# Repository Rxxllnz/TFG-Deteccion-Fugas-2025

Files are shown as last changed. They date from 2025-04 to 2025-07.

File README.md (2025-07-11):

# Detección de Fugas

Este Trabajo Fin de Grado documenta el proceso de puesta en funcionamiento y mejora de una planta automatizada, diseñada para simular una estación de servicio con el fin de generar datos útiles para la detección de fugas en depósitos subterráneos. A pesar de que el sistema había sido desarrollado en proyectos anteriores, presentaba múltiples errores de hardware y software que impedían su operatividad.

A lo largo del proyecto se identificaron y resolvieron fallos críticos como interferencias electromagnéticas, problemas de alimentación en los relés, lecturas inestables en sensores HX711, gestión incorrecta de volúmenes aleatorios y errores en la comunicación serie. Para su diagnóstico y corrección se implementaron herramientas de depuración propias, se mejoró la estructura del código y se aplicaron medidas físicas como el uso de cable apantallado, la separación de líneas sensibles y otras medidas que se detallarán a lo largo de la memoria.

Finalmente, se llevó a cabo el montaje definitivo del sistema incluyendo una caja eléctrica con bornas, carriles DIN y protecciones adecuadas, dejando la planta en un estado funcional, seguro y mantenible. El sistema ha sido validado mediante pruebas prolongadas y condiciones variables, demostrando su robustez y estabilidad. Este trabajo sienta una base sólida para futuros desarrollos orientados a la detección de fugas y a la docencia en entornos de automatización industrial.

### Memoria

Para mas información se incluye la memoria realizada para este Trabajo de Fin de Grado.

### Video demostrativo con explicación

(https://www.youtube.com/watch?v=KFtrlcwrUrw)

### Video demostrativo de 10 min de simulación

(https://www.youtube.com/watch?v=p-8AencXYqs)

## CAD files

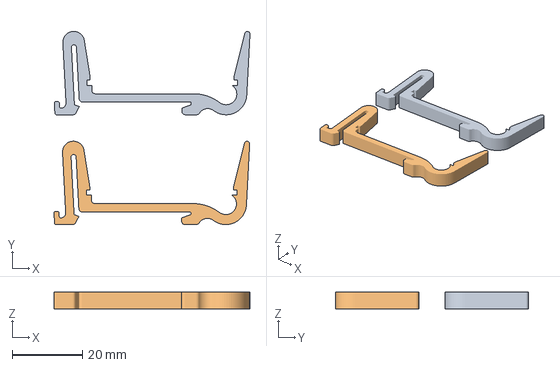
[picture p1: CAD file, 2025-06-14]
Montura Peristaltica.3mf
55.7 x 54.9 x 4.75 mm
MOSFET_Mount.stl x 2

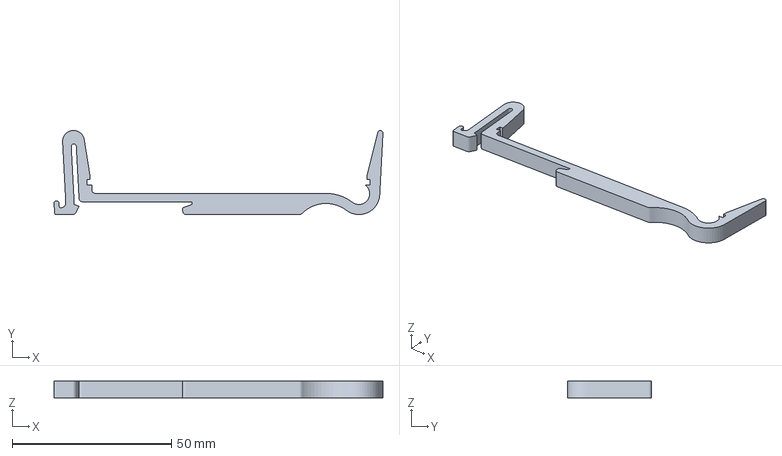
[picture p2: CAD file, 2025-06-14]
Montura Relés.3mf
103.3 x 26.4 x 5.29 mm

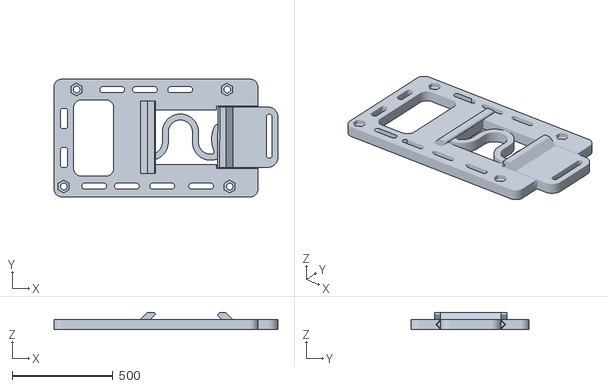
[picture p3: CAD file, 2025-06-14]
Montura Arduino Mega DIN.stl
1113.9 x 586.3 x 85.0

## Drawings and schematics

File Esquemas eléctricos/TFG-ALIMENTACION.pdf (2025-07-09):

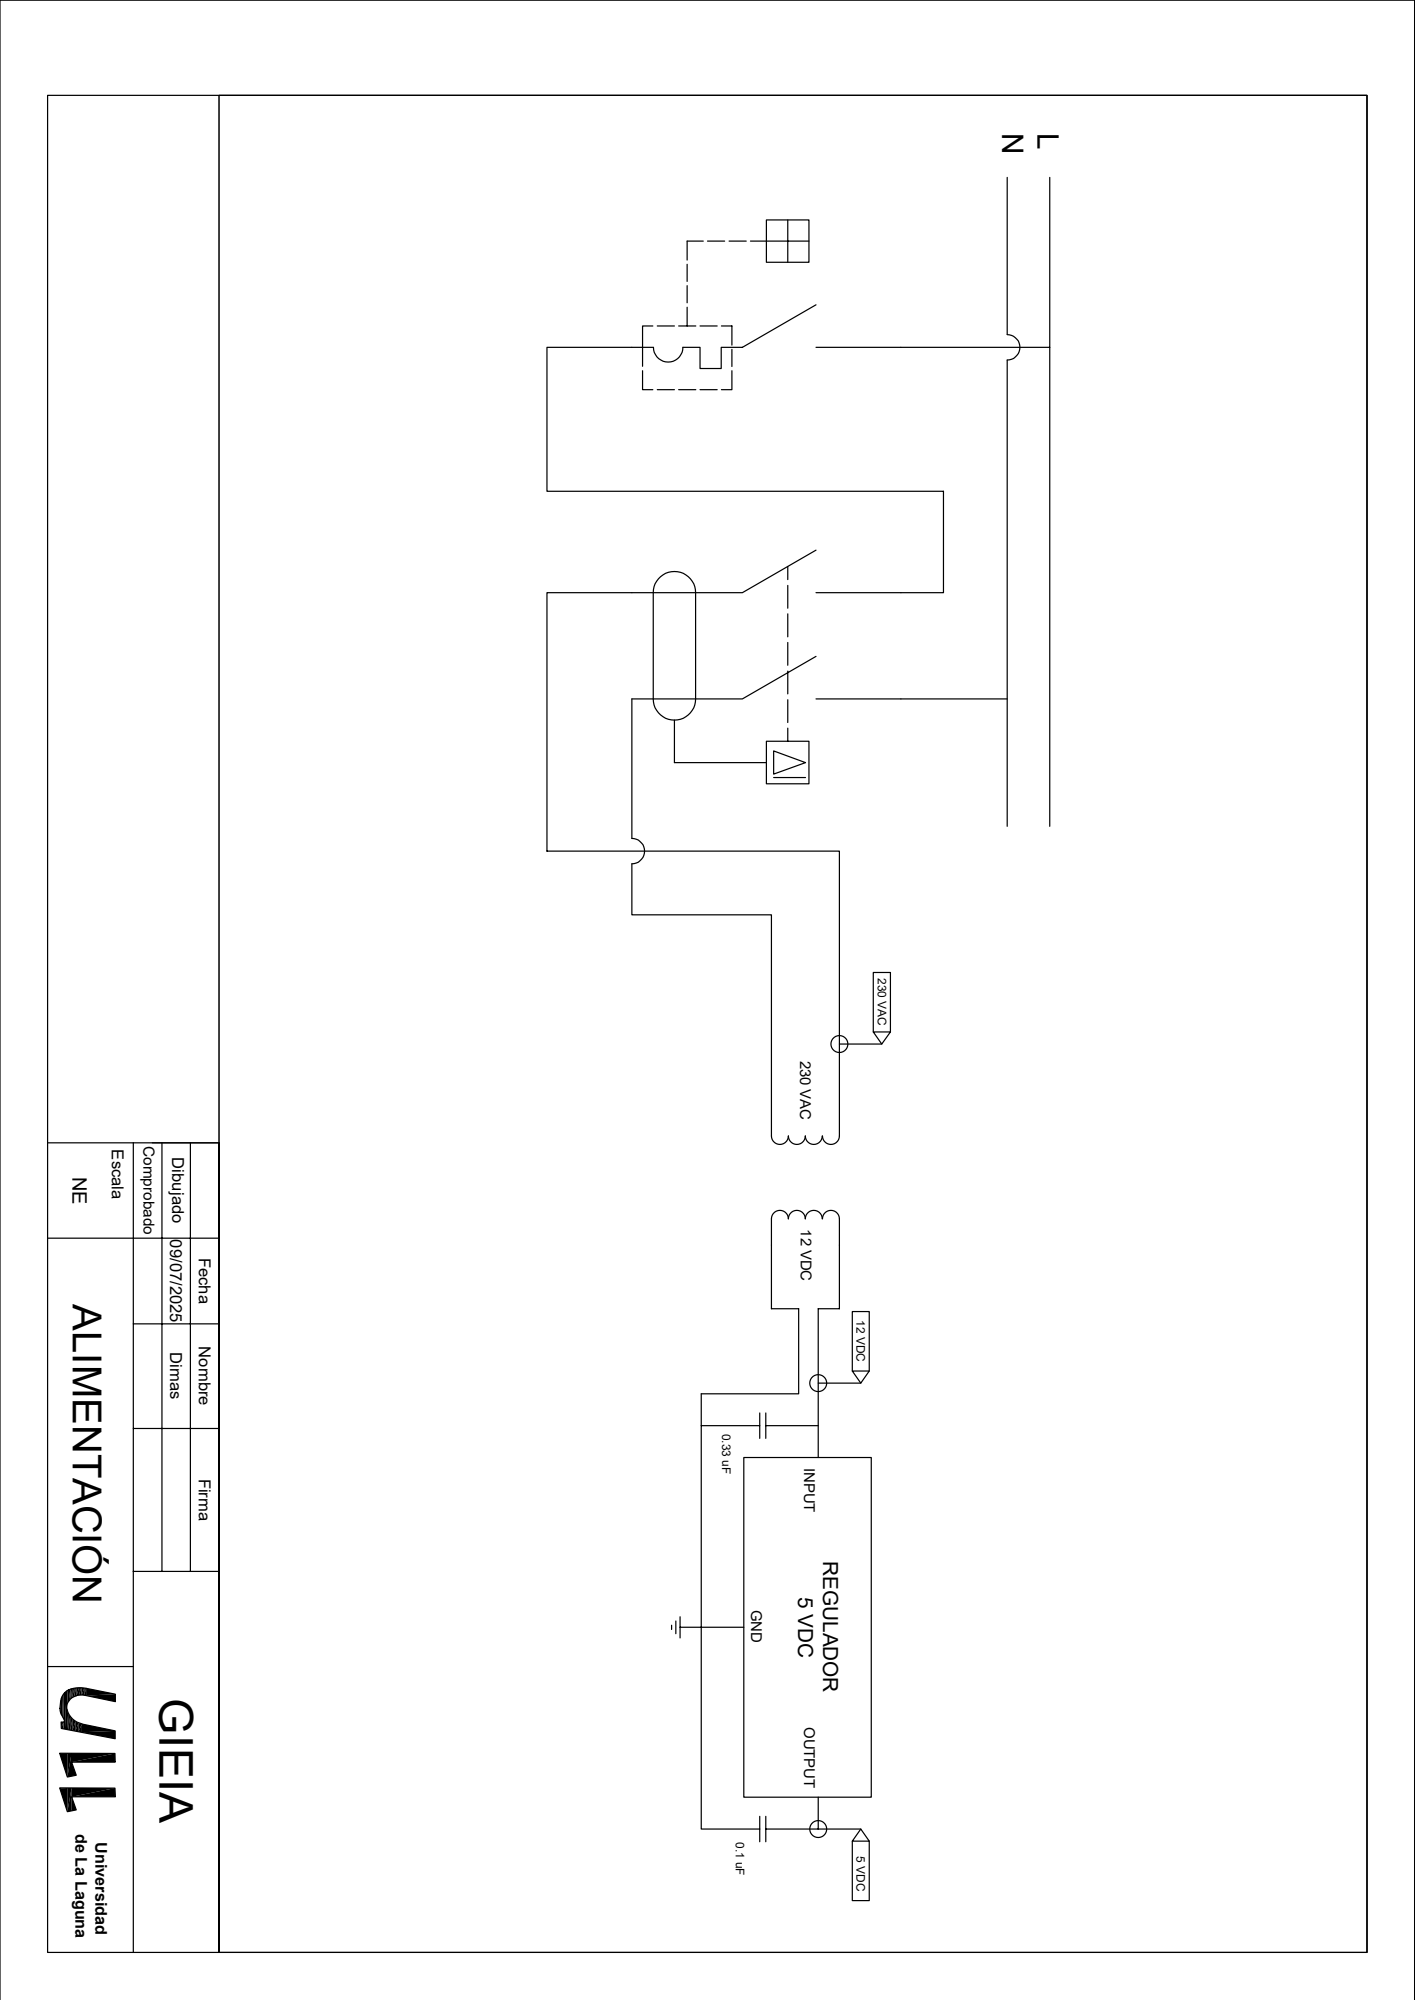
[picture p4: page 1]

NL INPUT OUTPUT GND REGULADOR 5 VDC 12 VDC 5 VDC 0.33 uF 0.1 uF 230 VAC 12 VDC 230 VAC Fecha Nombre Firma Dibujado Escala Comprobado 09/07/2025 Dimas NE ALIMENTACIÓN GIEIA Universidad de La Laguna

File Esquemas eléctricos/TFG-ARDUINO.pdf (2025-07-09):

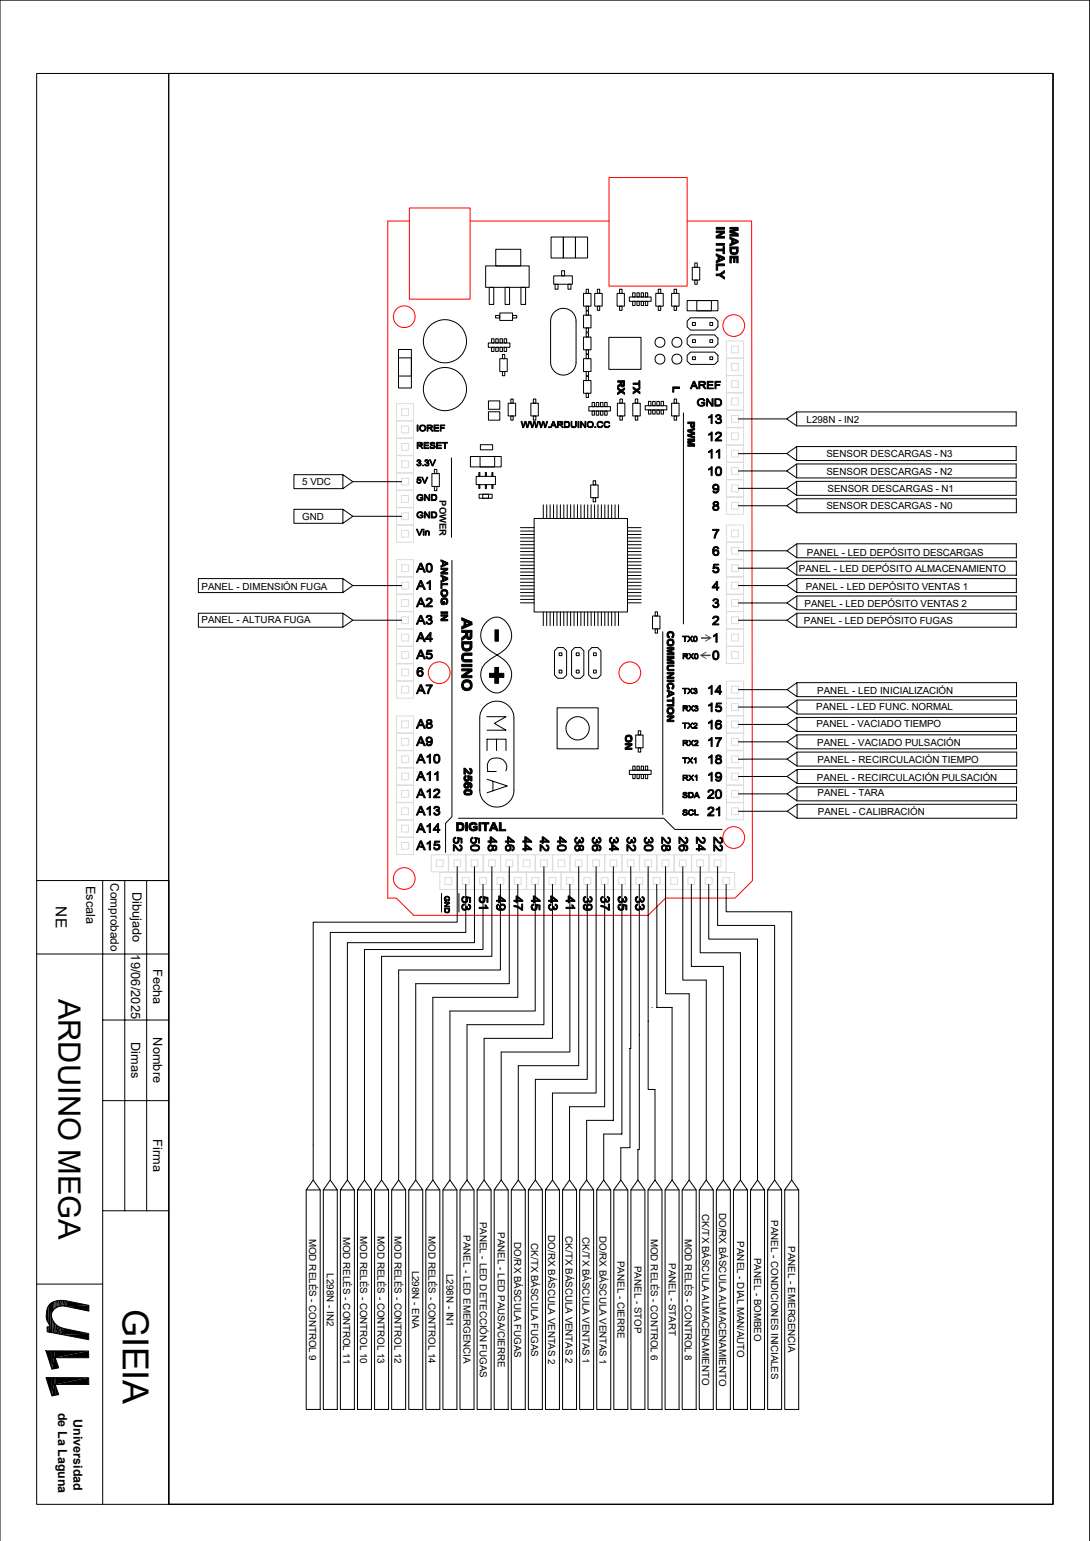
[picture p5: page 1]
POWER; 5 VDC; GND; PANEL - ALTURA FUGA; PANEL - LED DEPÓSITO FUGAS; SENSOR DESCARGAS - N0; SENSOR DESCARGAS - N1; SENSOR DESCARGAS - N2; SENSOR DESCARGAS - N3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

PANEL - LED DEPÓSITO DESCARGAS
PANEL - LED DEPÓSITO ALMACENAMIENTO
PANEL - LED DEPÓSITO VENTAS 1
PANEL - LED DEPÓSITO VENTAS 2

PANEL - DIMENSIÓN FUGA

PANEL - LED INICIALIZACIÓN
PANEL - LED FUNC. NORMAL
PANEL - VACIADO TIEMPO
PANEL - VACIADO PULSACIÓN
PANEL - RECIRCULACIÓN TIEMPO
PANEL - RECIRCULACIÓN PULSACIÓN
PANEL - TARA

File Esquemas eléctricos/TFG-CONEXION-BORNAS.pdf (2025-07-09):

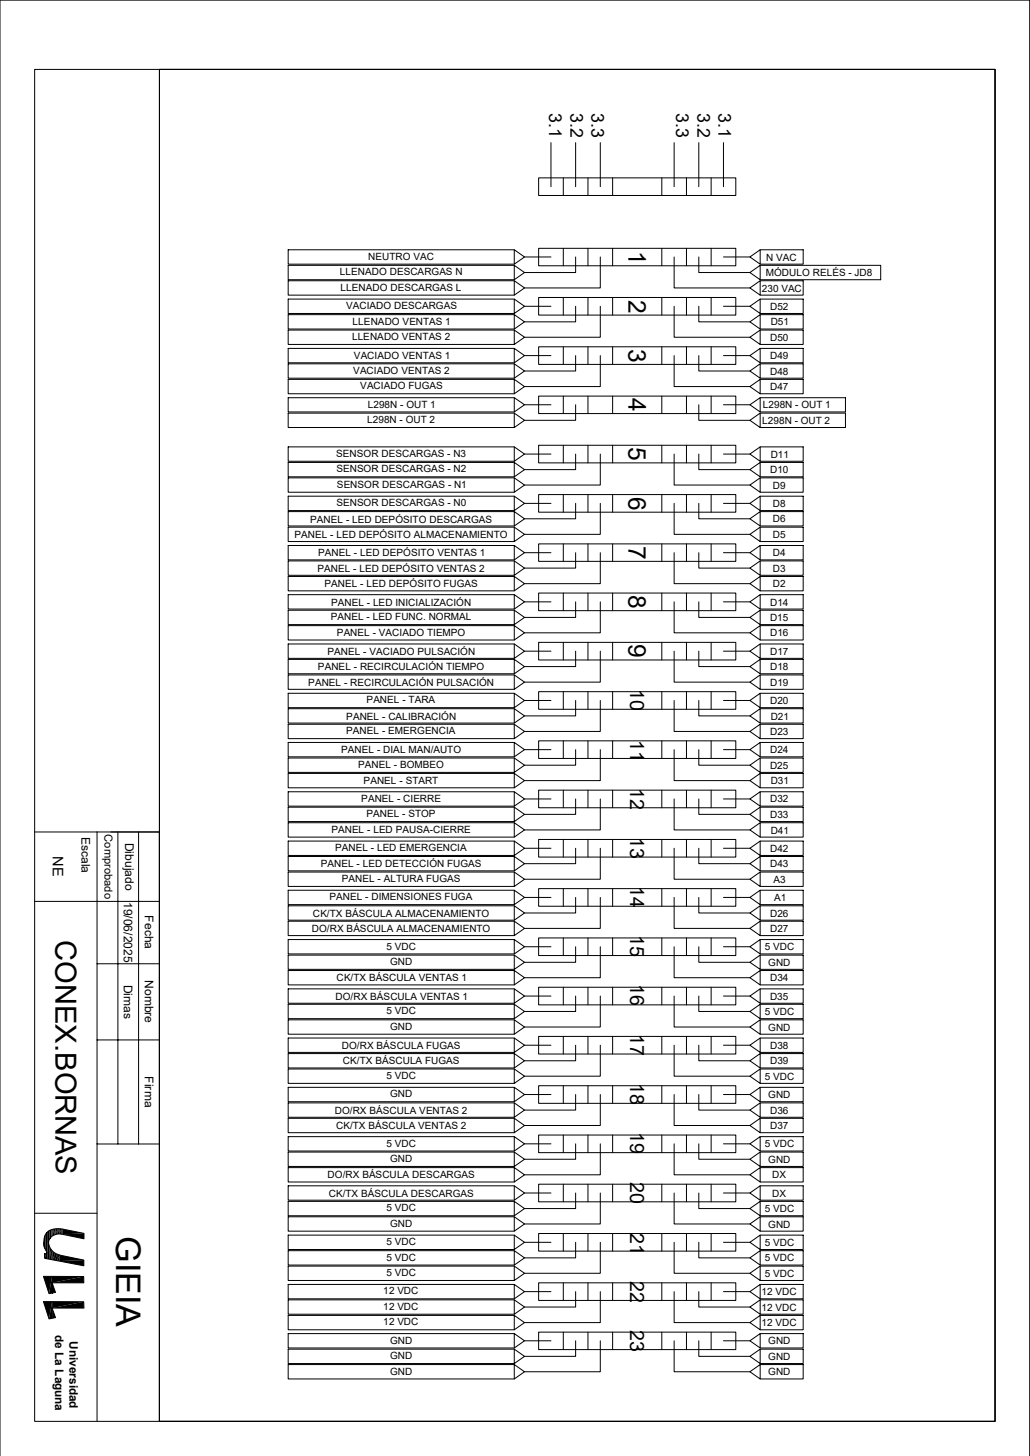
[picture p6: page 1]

SENSOR DESCARGAS - N3
SENSOR DESCARGAS - N2
SENSOR DESCARGAS - N1
SENSOR DESCARGAS - N0
PANEL - LED DEPÓSITO DESCARGAS
PANEL - LED DEPÓSITO VENTAS 1
PANEL - LED DEPÓSITO VENTAS 2
PANEL - LED DEPÓSITO FUGAS
PANEL - LED INICIALIZACIÓN
PANEL - LED FUNC. NORMAL
PANEL - VACIADO PULSACIÓN
PANEL - RECIRCULACIÓN TIEMPO
PANEL - RECIRCULACIÓN PULSACIÓN

PANEL - TARA
PANEL - CALIBRACIÓN
PANEL - DIAL MAN/AUTO
PANEL - BOMBEO
PANEL - START
PANEL - CIERRE
PANEL - STOP

PANEL - LED PAUSA-CIERRE
PANEL - LED EMERGENCIA
PANEL - LED DETECCIÓN FUGAS
PANEL - ALTURA FUGAS
PANEL - DIMENSIONES FUGA
CK/TX BÁSCULA ALMACENAMIENTO
DO/RX BÁSCULA ALMACENAMIENTO

CK/TX BÁSCULA VENTAS 1
DO/RX BÁSCULA VENTAS 1

DO/RX BÁSCULA FUGAS
CK/TX BÁSCULA FUGAS

DO/RX BÁSCULA VENTAS 2

DO/RX BÁSCULA DESCARGAS
CK/TX BÁSCULA DESCARGAS

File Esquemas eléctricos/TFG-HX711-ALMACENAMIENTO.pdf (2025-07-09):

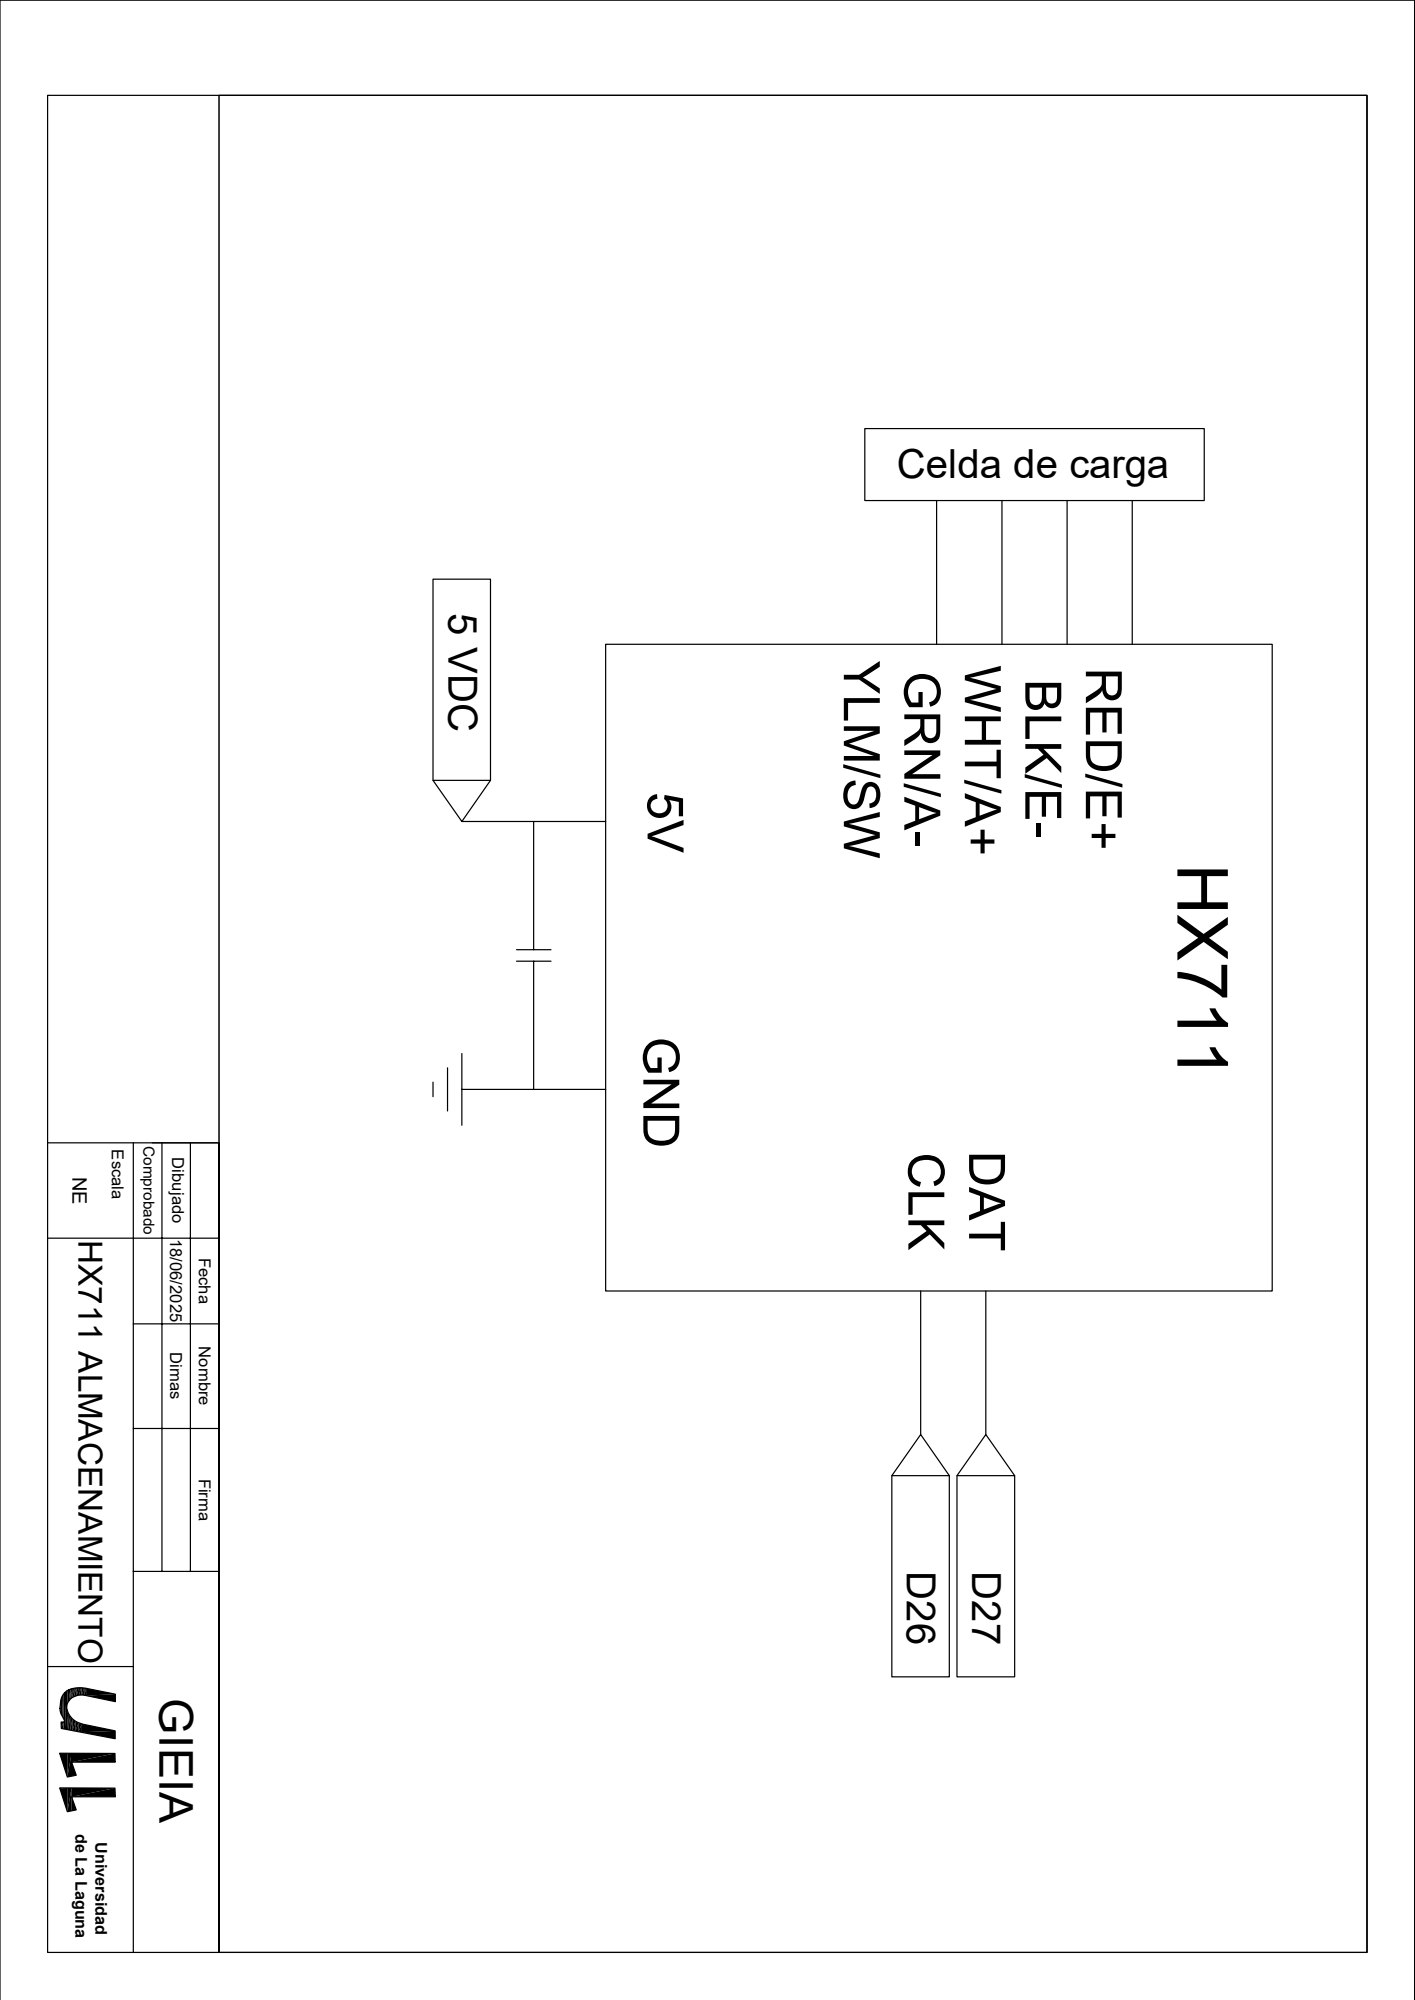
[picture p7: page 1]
Celda de carga Fecha Nombre Firma Dibujado Escala; Comprobado; 18/06/2025 Dimas NE HX711 ALMACENAMIENTO; GIEIA Universidad de La Laguna

5V GND YLM/SW GRN/A- WHT/A+ BLK/E- RED/E+ CLK DAT 5 VDC D26 D27

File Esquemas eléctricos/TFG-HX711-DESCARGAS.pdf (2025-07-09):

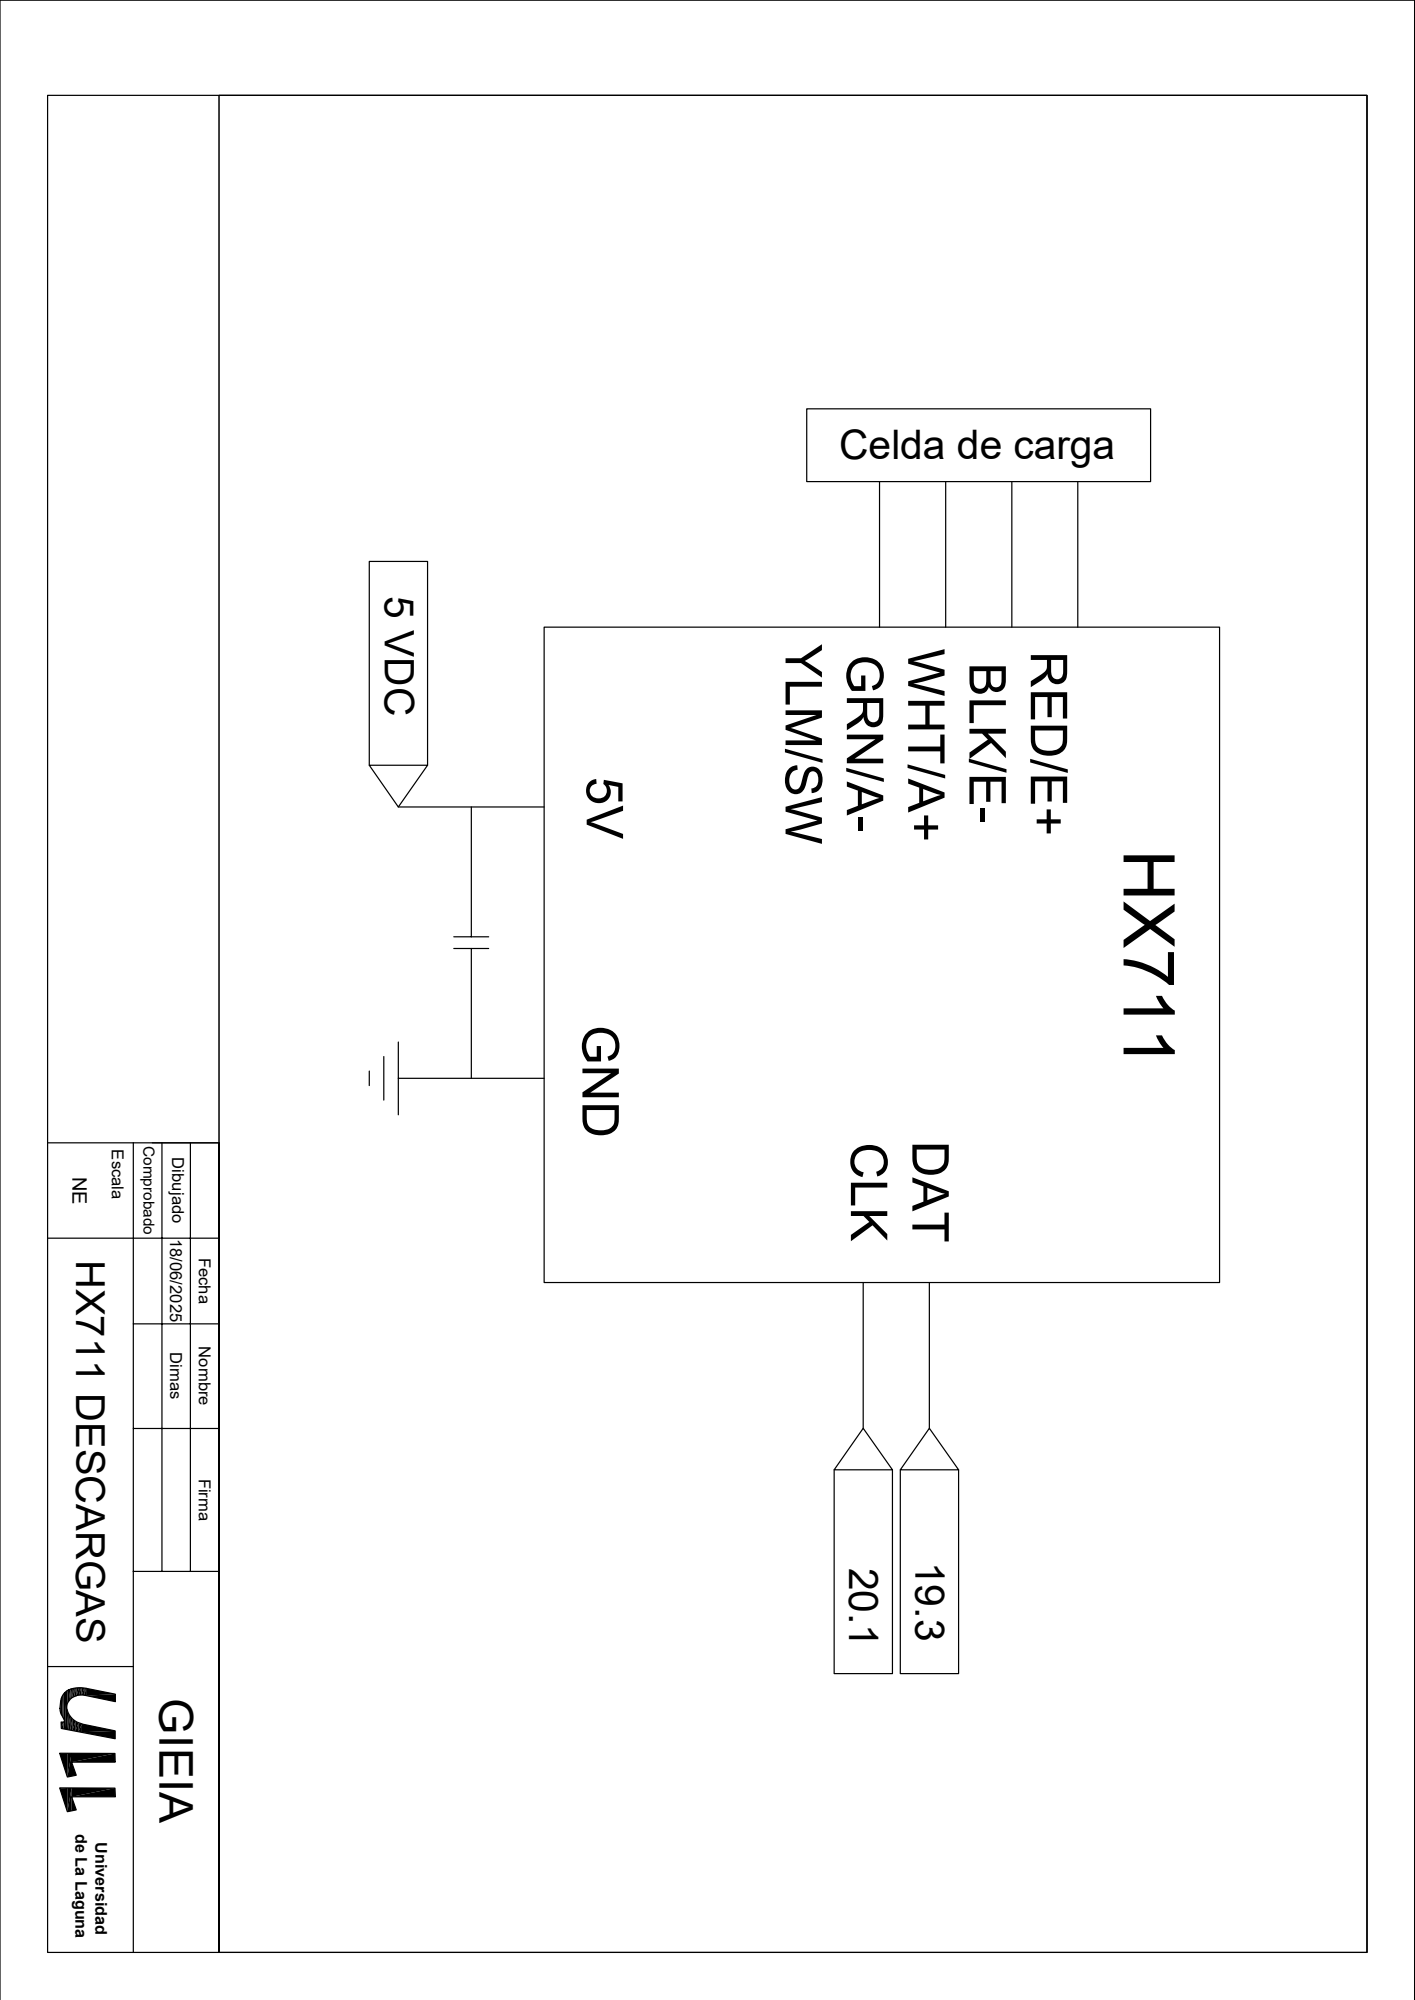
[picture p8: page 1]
Celda de carga Fecha Nombre Firma Dibujado Escala; Comprobado; 18/06/2025 Dimas NE HX711 DESCARGAS; GIEIA Universidad de La Laguna

5V GND YLM/SW GRN/A- WHT/A+ BLK/E- RED/E+ CLK DAT 5 VDC 20.1 19.3

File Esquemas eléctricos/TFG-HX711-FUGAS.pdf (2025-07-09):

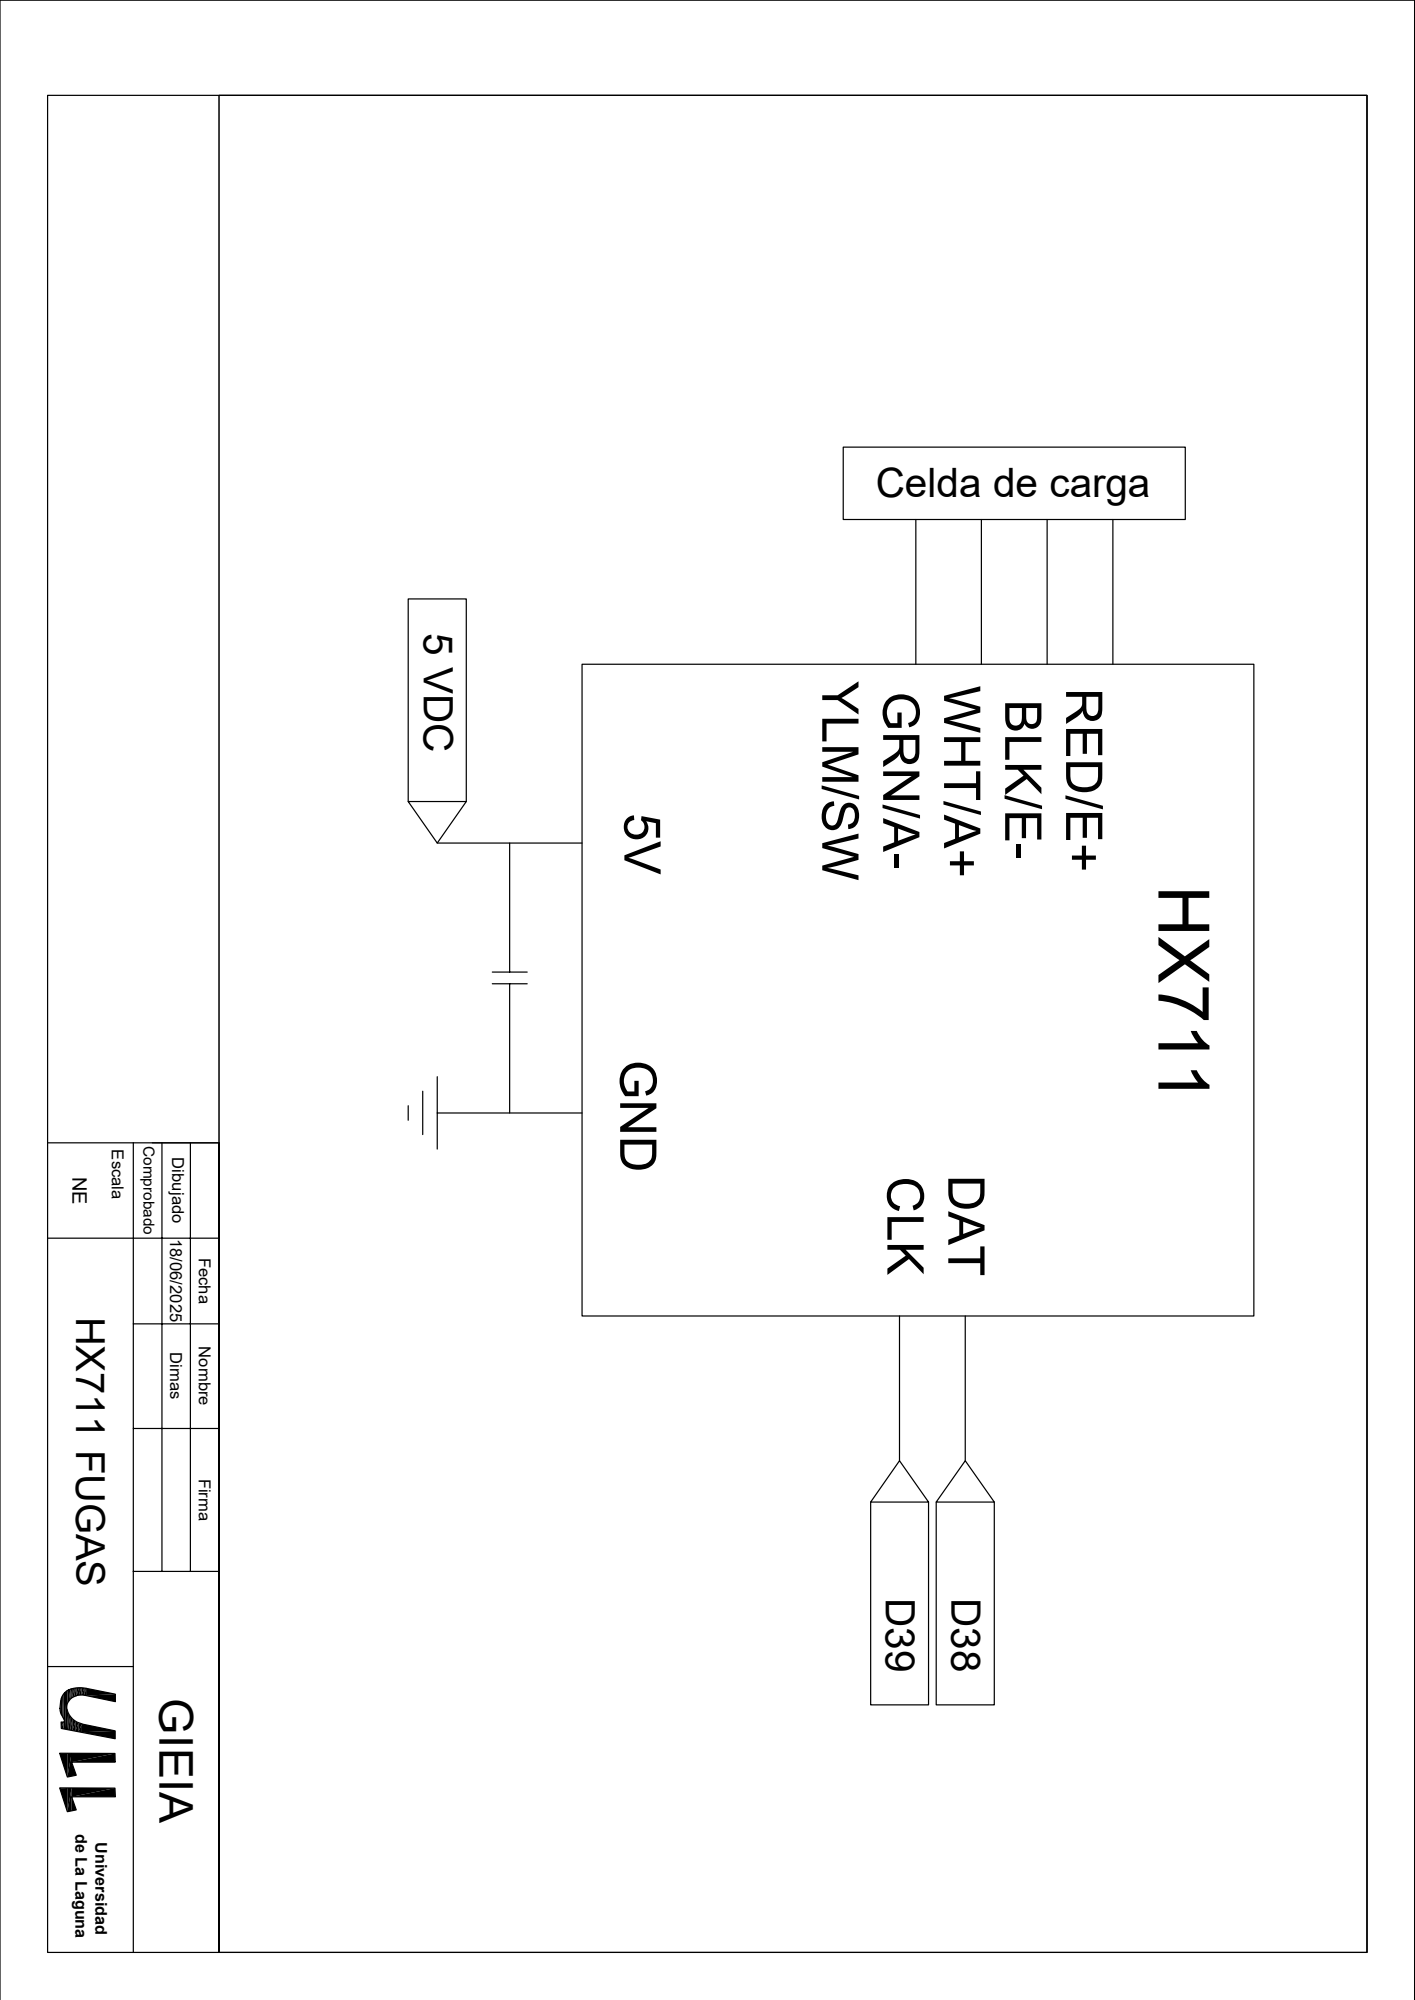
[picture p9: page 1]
Celda de carga Fecha Nombre Firma Dibujado Escala; Comprobado; 18/06/2025 Dimas NE HX711 FUGAS; GIEIA Universidad de La Laguna

5V GND YLM/SW GRN/A- WHT/A+ BLK/E- RED/E+ CLK DAT 5 VDC D39 D38

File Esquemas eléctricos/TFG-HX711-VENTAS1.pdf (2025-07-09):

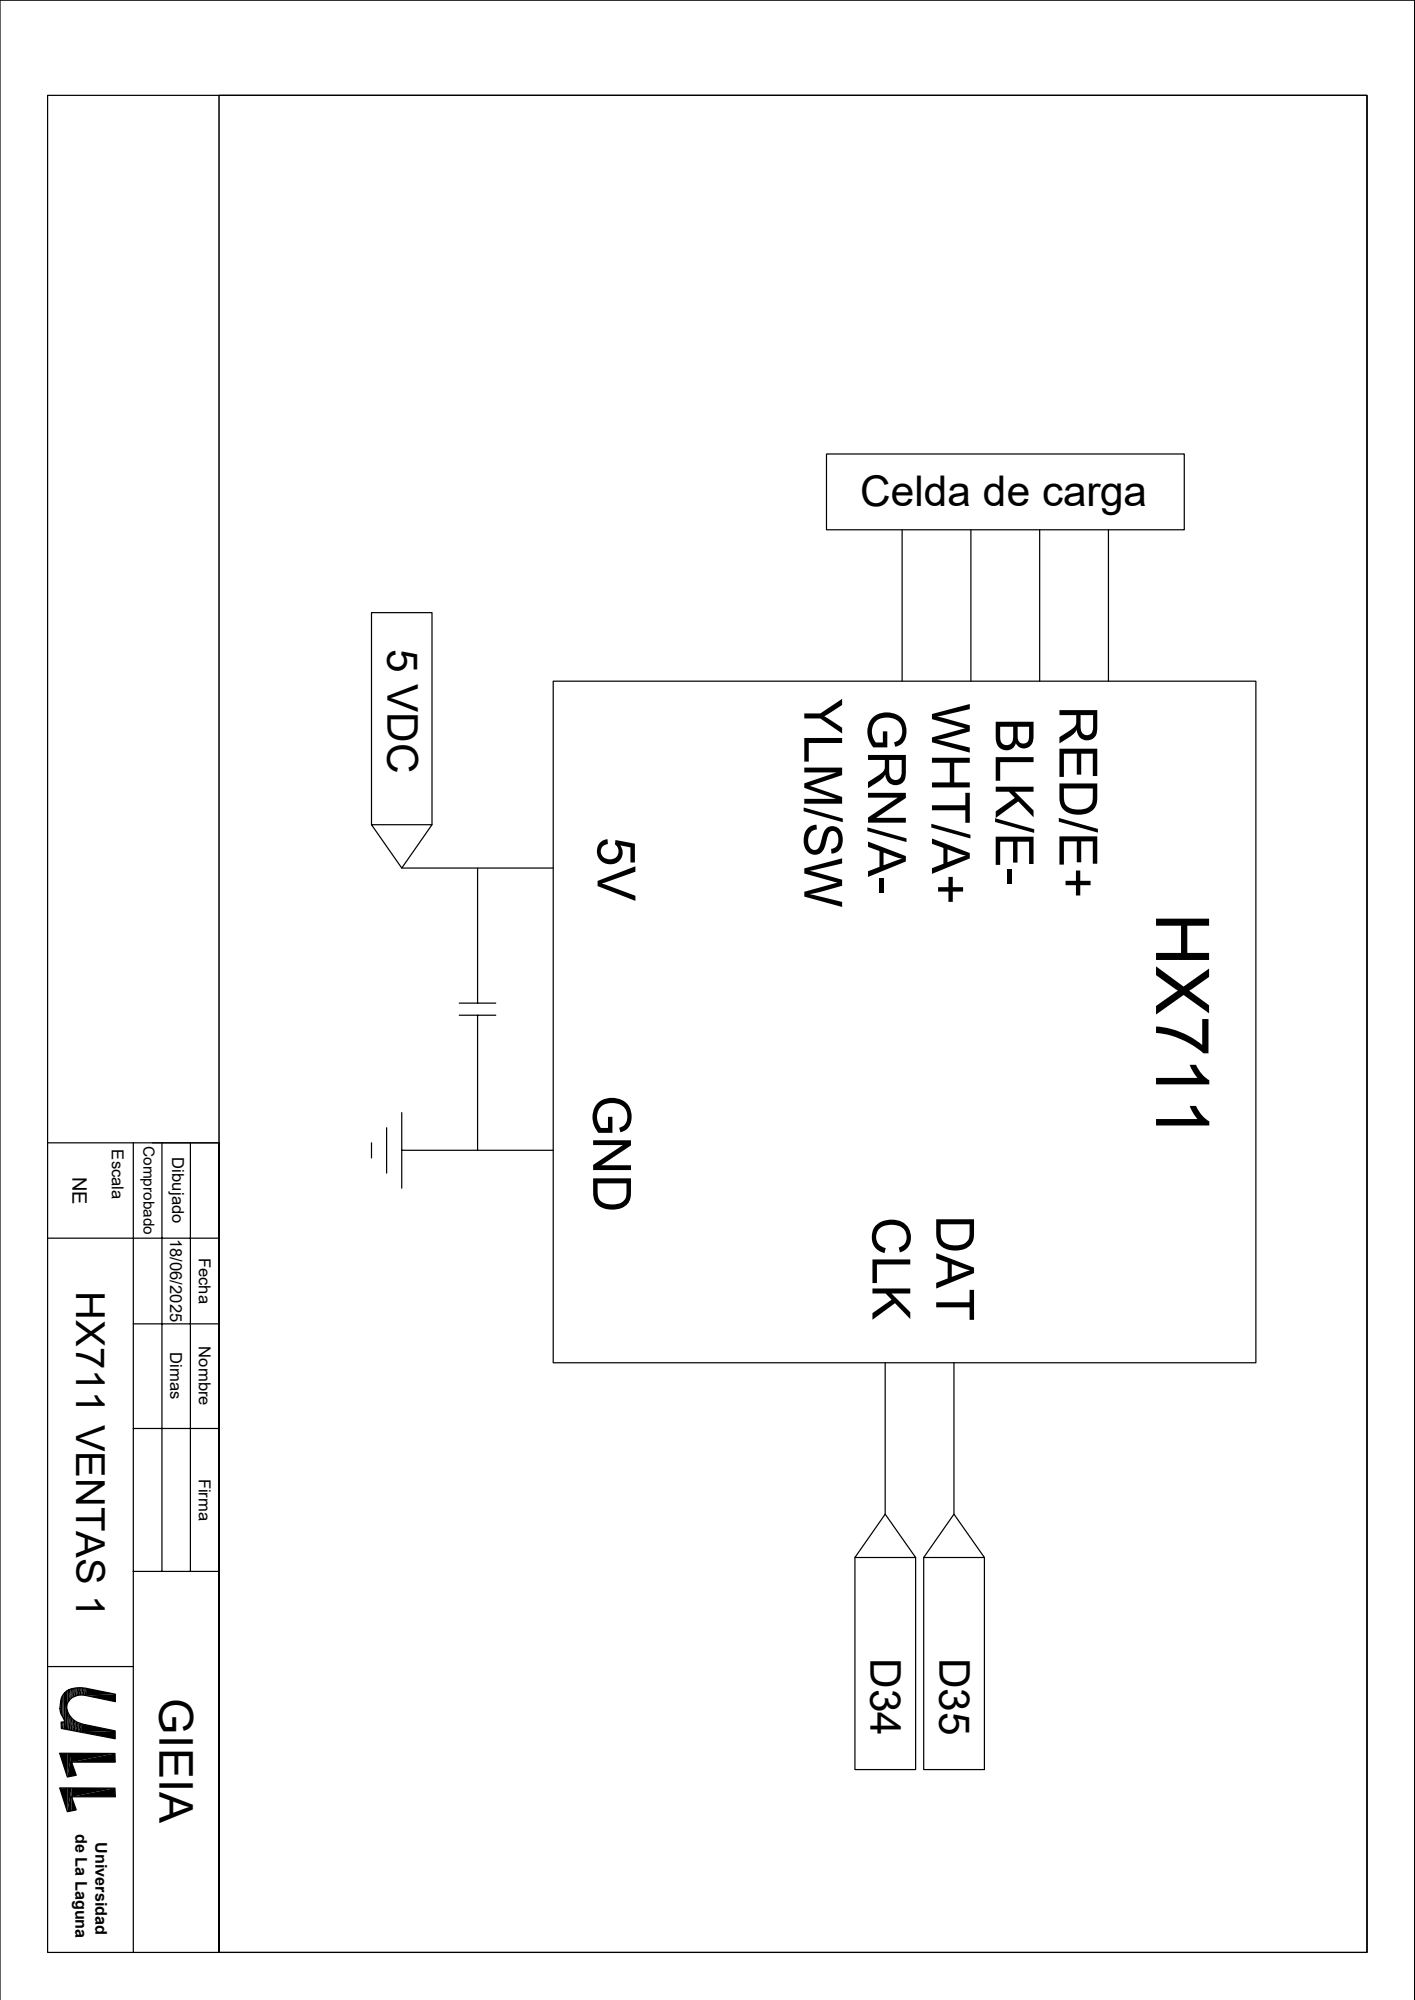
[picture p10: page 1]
Celda de carga Fecha Nombre Firma Dibujado Escala; Comprobado; 18/06/2025 Dimas NE HX711 VENTAS 1; GIEIA Universidad de La Laguna

5V GND YLM/SW GRN/A- WHT/A+ BLK/E- RED/E+ CLK DAT 5 VDC D34 D35

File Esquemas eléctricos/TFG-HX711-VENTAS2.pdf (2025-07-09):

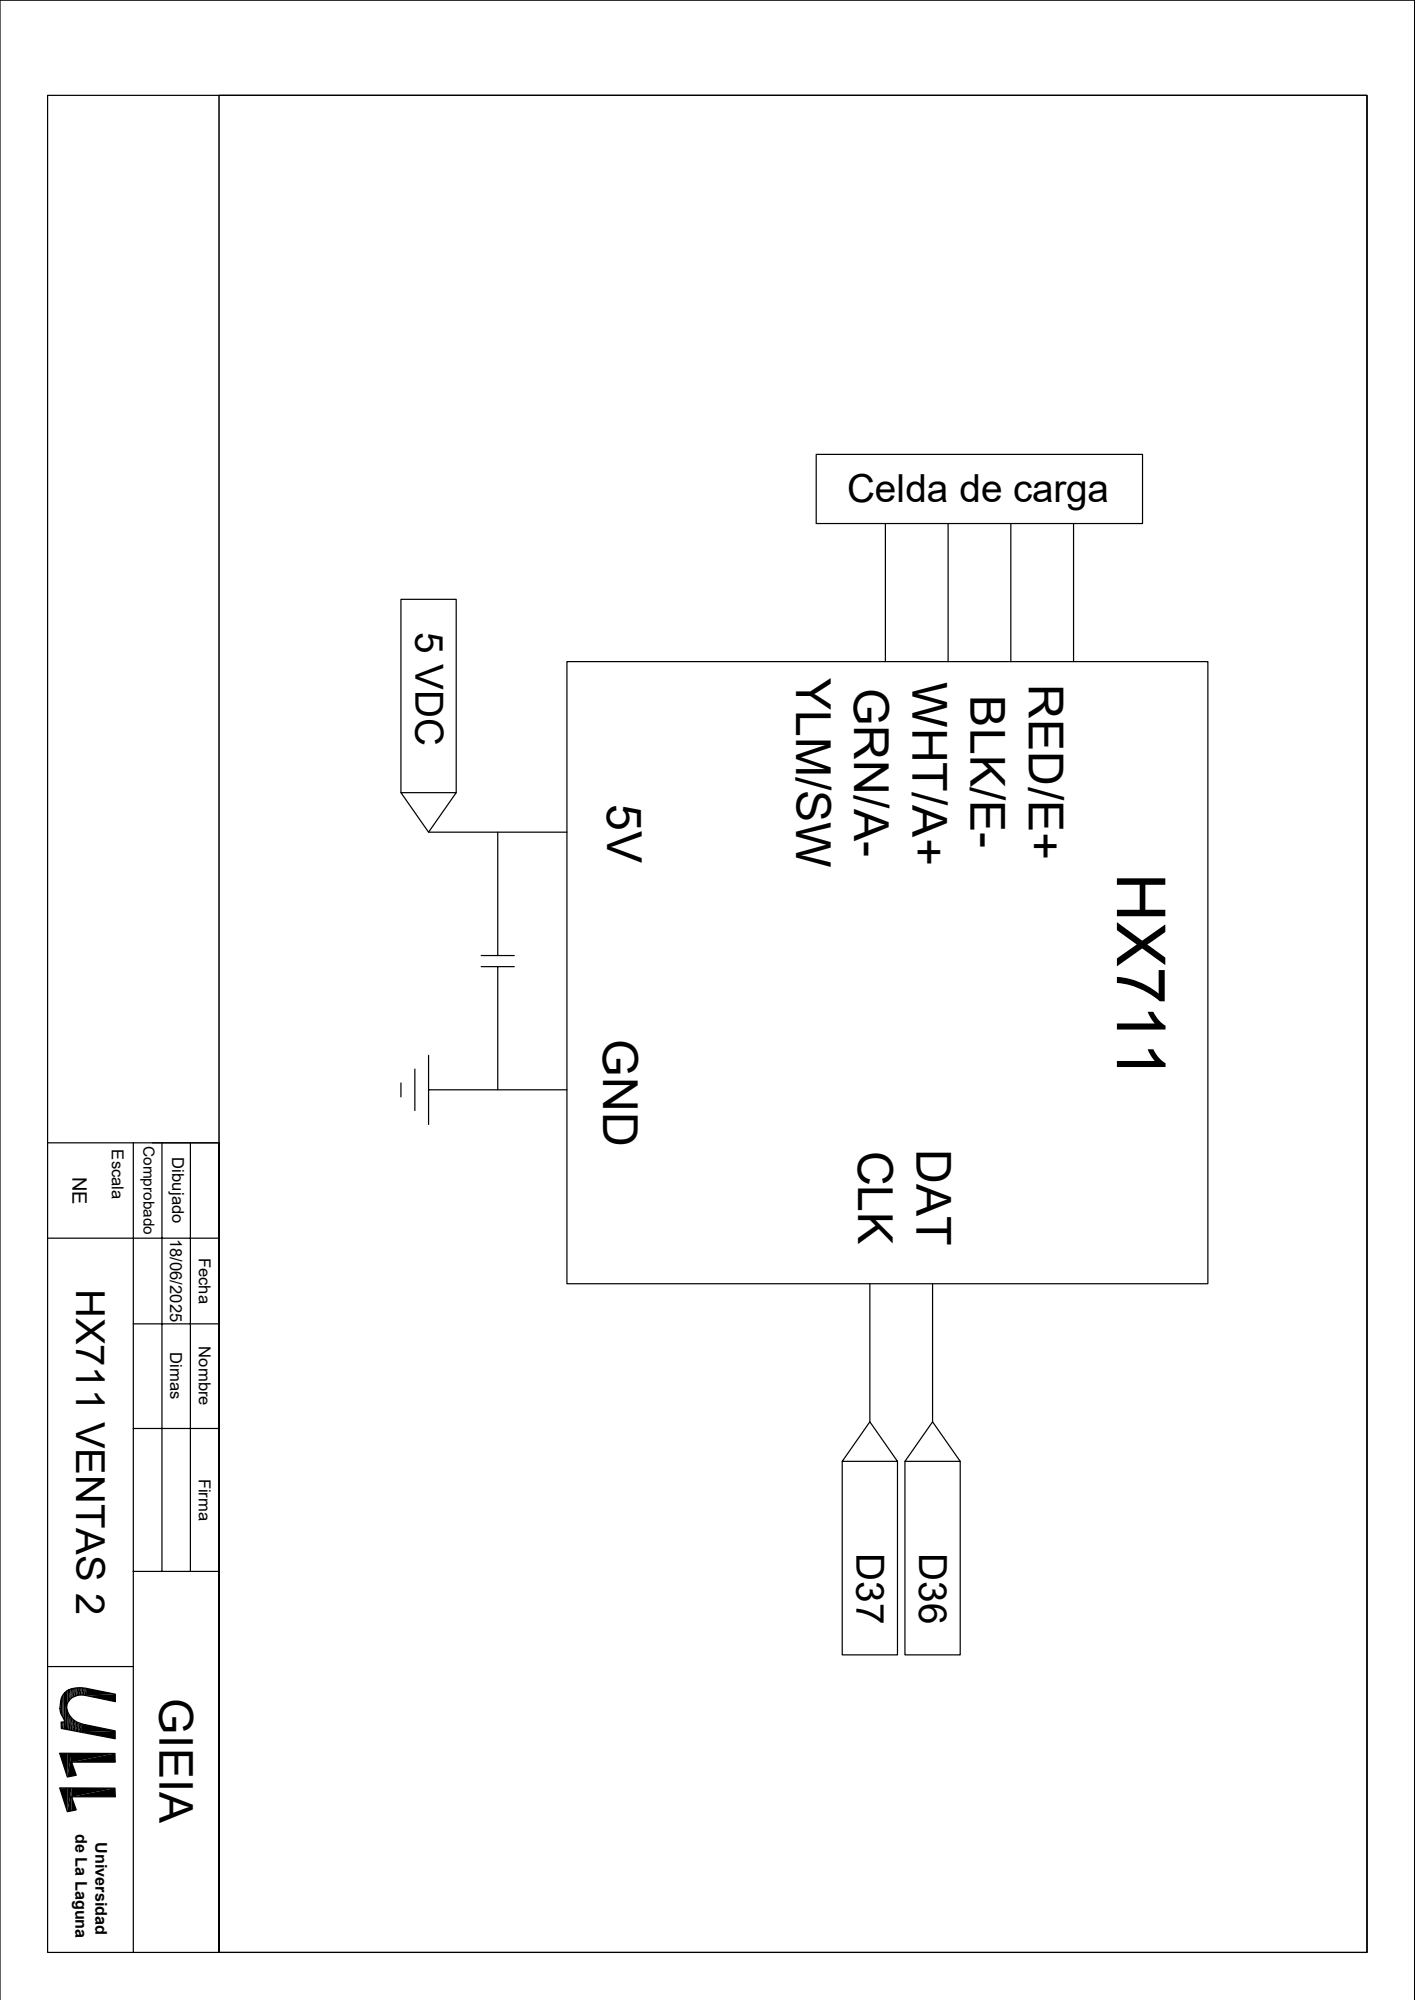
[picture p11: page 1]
Celda de carga Fecha Nombre Firma Dibujado Escala; Comprobado; 18/06/2025 Dimas NE HX711 VENTAS 2; GIEIA Universidad de La Laguna

5V GND YLM/SW GRN/A- WHT/A+ BLK/E- RED/E+ CLK DAT 5 VDC D37 D36

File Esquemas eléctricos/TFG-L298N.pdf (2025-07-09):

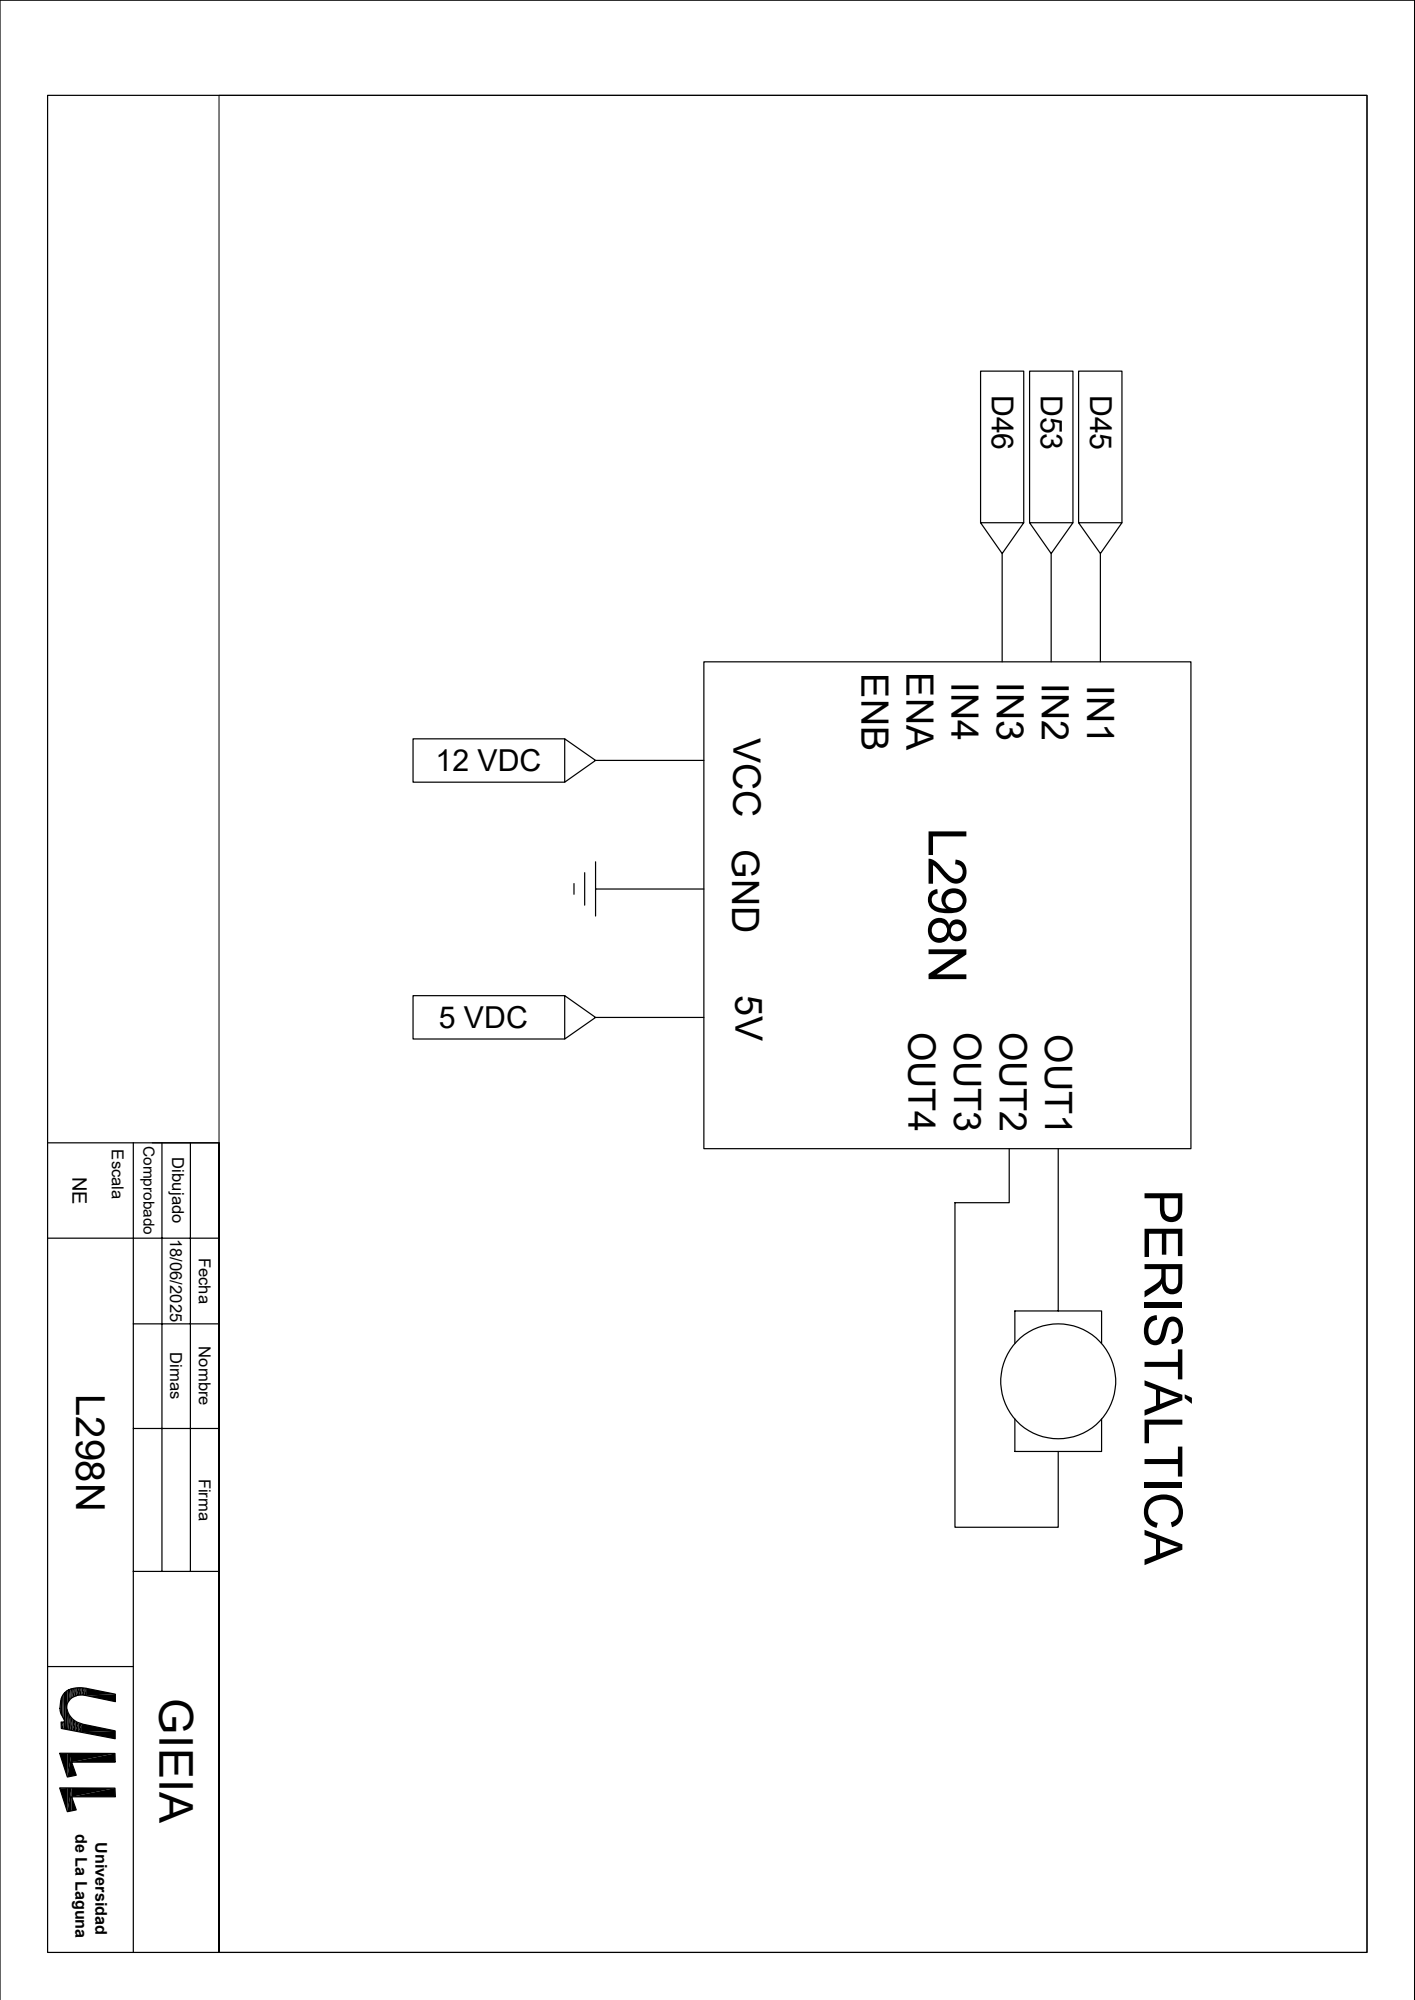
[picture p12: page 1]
5 VDC; 12 VDC; PERISTÁLTICA D46 D53 D45 Fecha Nombre Firma Dibujado Escala; Comprobado; 18/06/2025 Dimas NE L298N; GIEIA Universidad de La Laguna

VCC 5V GND IN4 IN3 IN2 IN1 ENB ENA OUT4 OUT3 OUT2 OUT1 L298N

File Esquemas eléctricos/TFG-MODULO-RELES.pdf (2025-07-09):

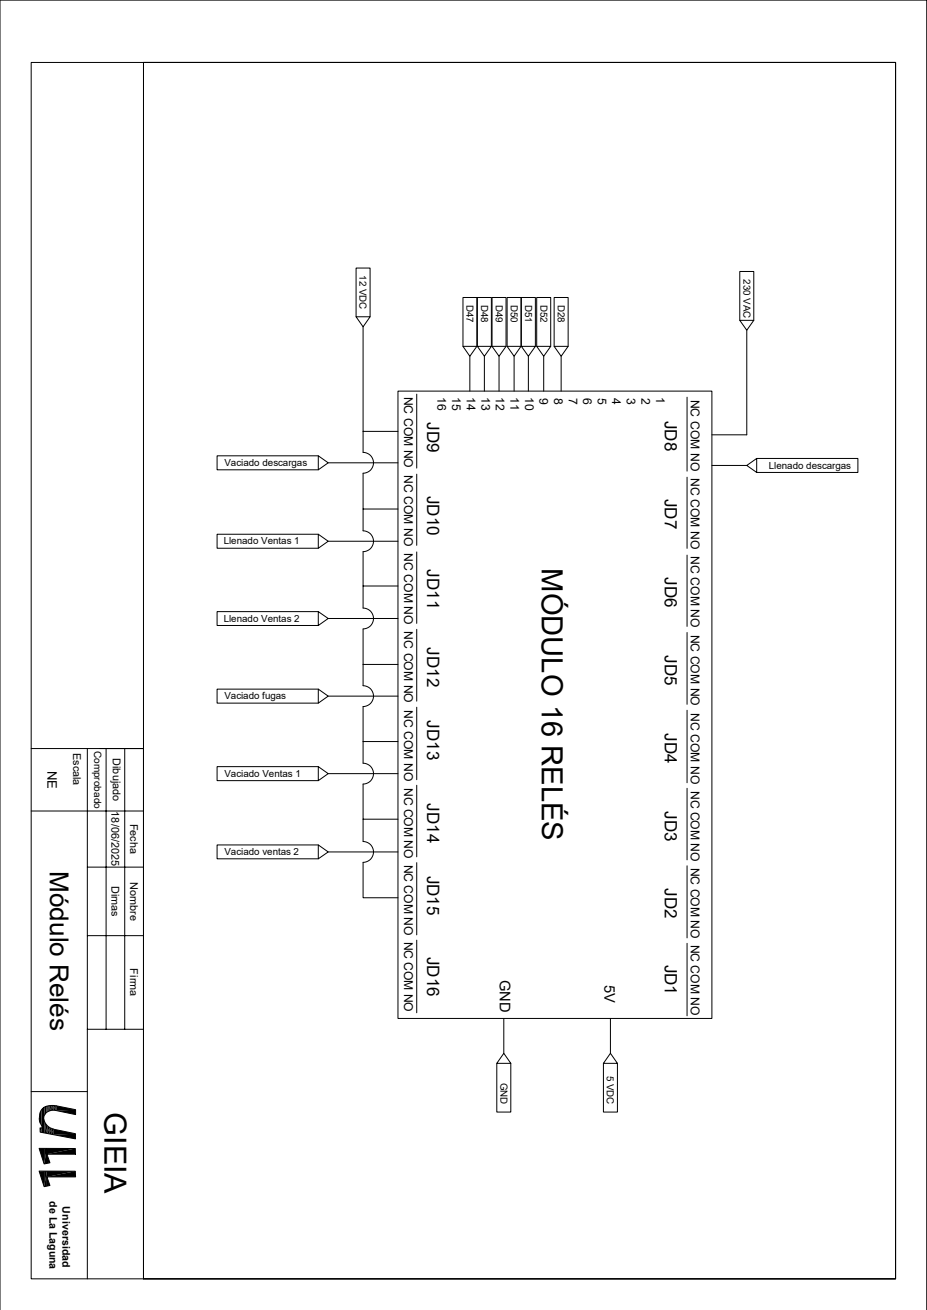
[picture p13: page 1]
Vaciado descargas; Llenado Ventas 1; Llenado Ventas 2; Vaciado fugas; Vaciado Ventas 1; Vaciado ventas 2; 230 VAC; Llenado descargas D47 D48 D49 D50 D51 D52; D28 Fecha Nombre Firma Dibujado Escala; Comprobado; 18/06/2025 Dimas NE Módulo Relés; GIEIA Universidad de La Laguna

1 MÓDULO 16 RELÉS 12 VDC 5 VDC GND

NC COM NO NC COM NO NC COM NO NC COM NO NC COM NO NC COM NO NC COM NO NC COM NO NC COM NO NC COM NO NC COM NO NC COM NO NC COM NO NC COM NO NC COM NO NC COM NO JD9 JD10 JD11 JD12 JD13 JD14 JD15 JD16 JD8 JD7 JD6 JD5 JD4 JD3 JD2 JD1GND 5V 16151413121110

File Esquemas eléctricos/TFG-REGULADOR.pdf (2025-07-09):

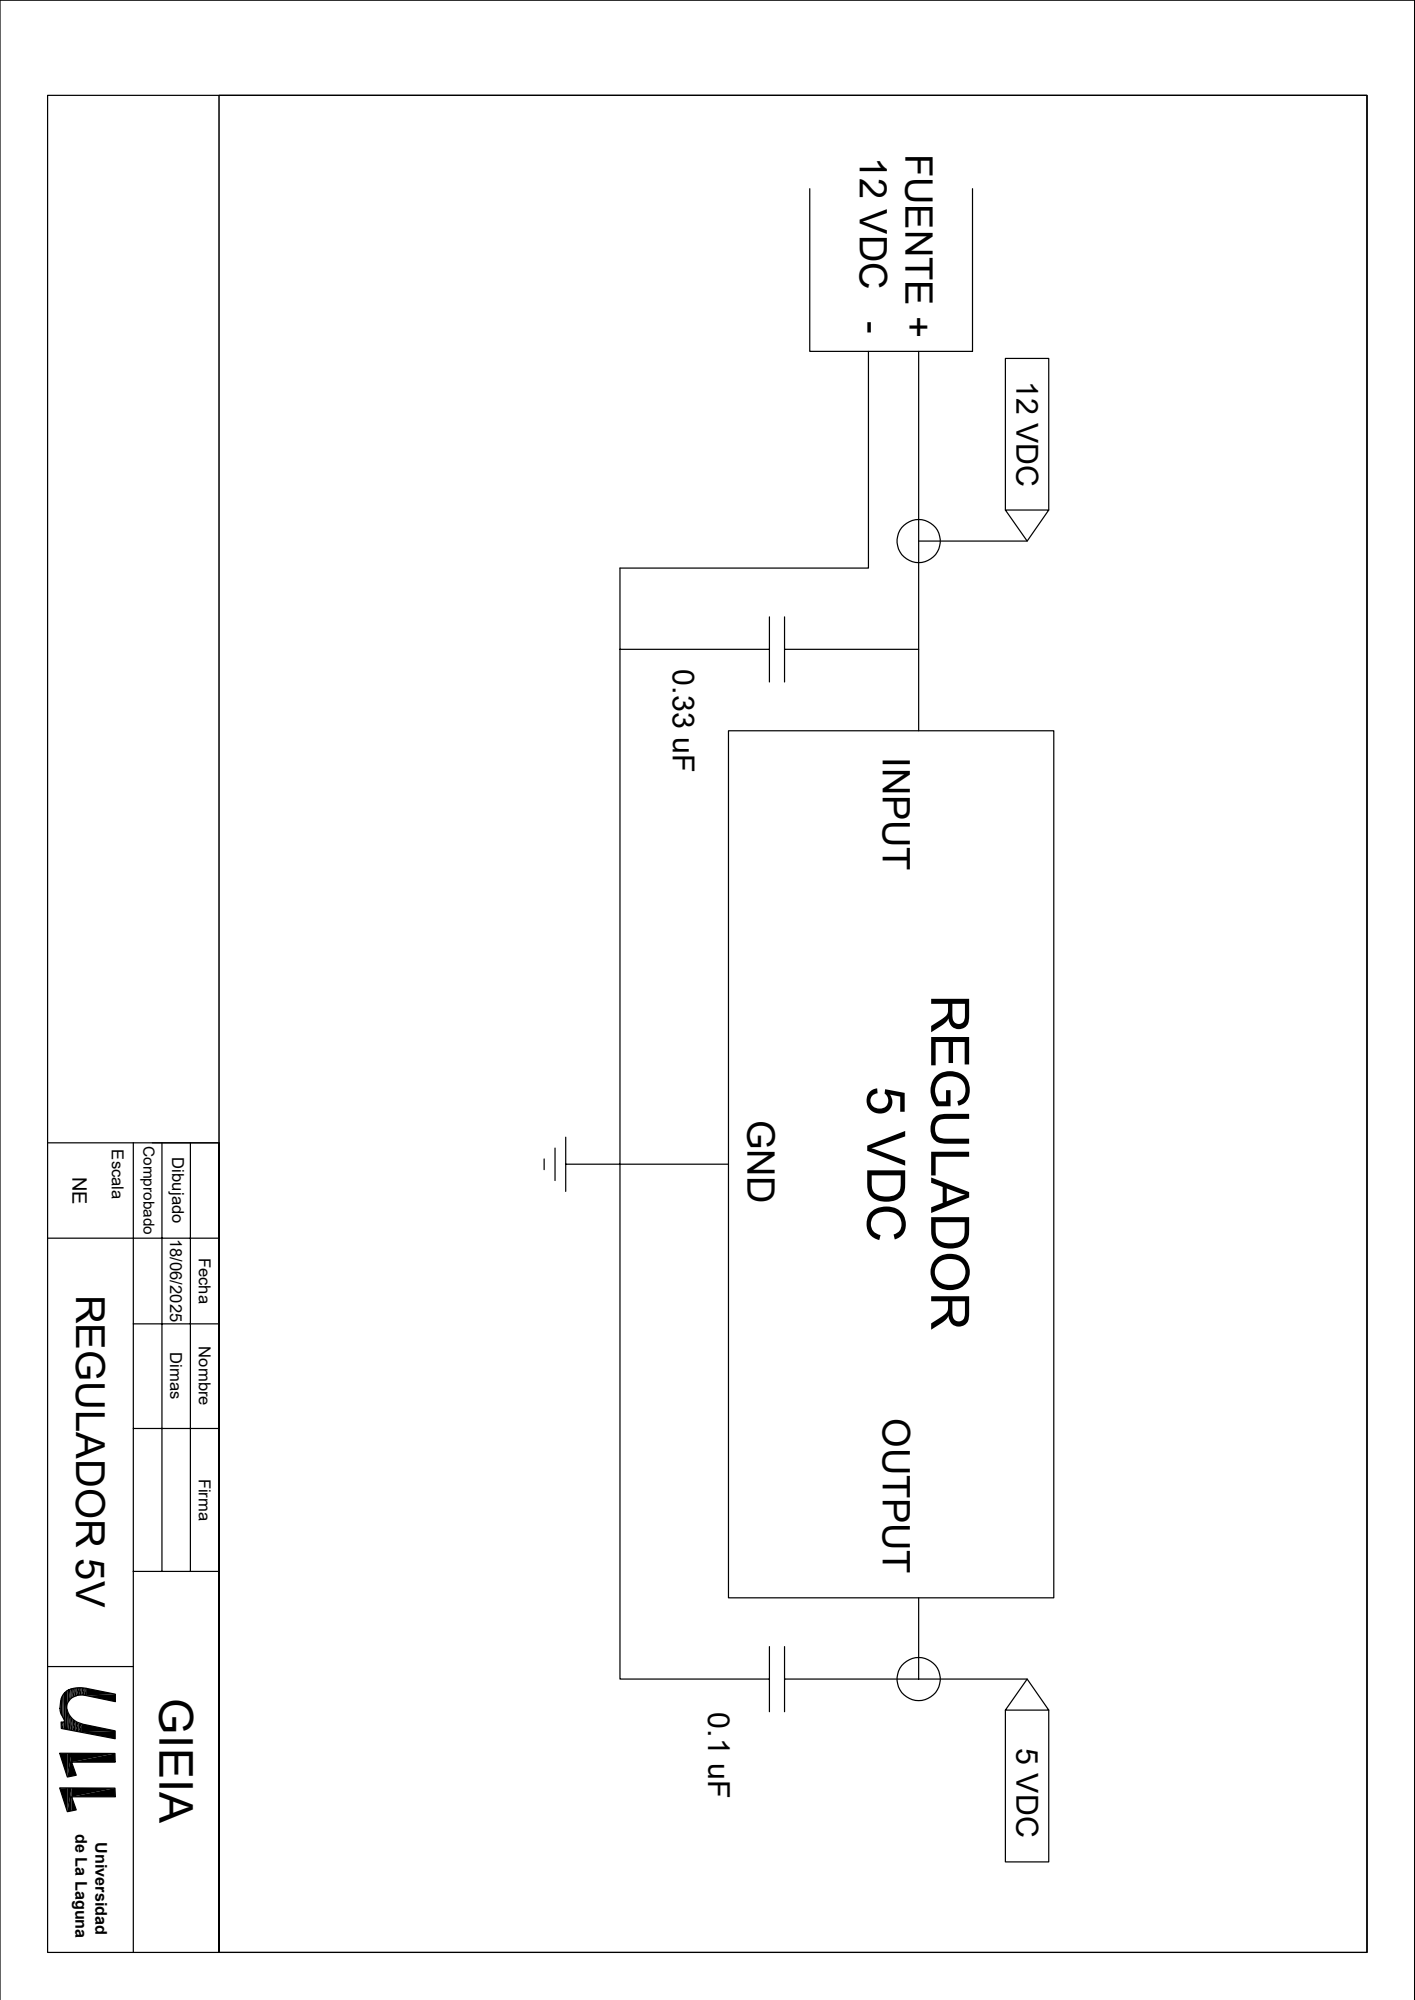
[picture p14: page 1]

INPUT OUTPUT 12 VDC - FUENTE + GND REGULADOR 5 VDC 12 VDC 5 VDC 0.33 uF 0.1 uF Fecha Nombre Firma Dibujado Escala Comprobado 18/06/2025 Dimas NE REGULADOR 5V GIEIA Universidad de La Laguna

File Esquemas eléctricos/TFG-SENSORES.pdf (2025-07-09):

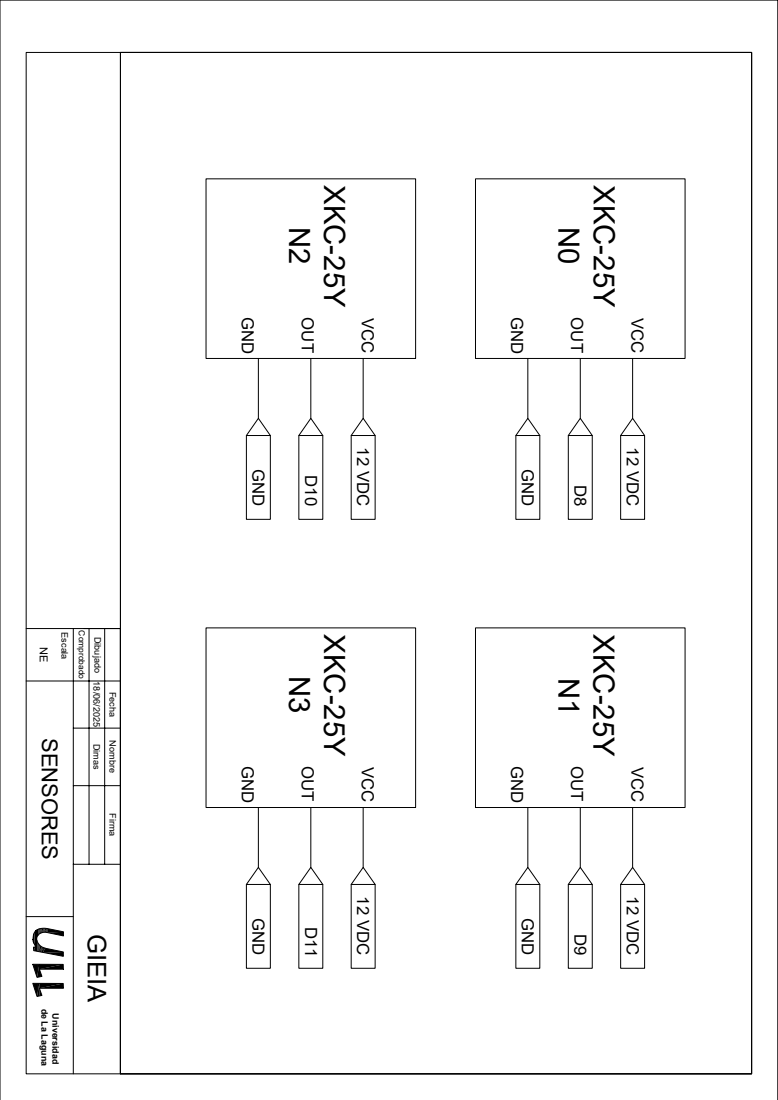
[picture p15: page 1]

XKC-25Y N0 12 VDCD8 GND GND OUT VCC XKC-25Y N2 12 VDC GND D10 GND OUT VCC XKC-25Y N1 12 VDCD9 GND GND OUT VCC XKC-25Y N3 12 VDC D11 GND GND OUT VCC Fecha Nombre Firma Dibujado Escala Comprobado 18/06/2025 Dimas NE SENSORES GIEIA Universidad de La Laguna

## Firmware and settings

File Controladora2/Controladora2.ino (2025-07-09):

#include "Controladora2.h"
#include "Deposito2.h"
#include "Debug.h"
#include "PanelControl.h"


#include <HX711_ADC.h>
#if defined(ESP8266)|| defined(ESP32) || defined(AVR)
#include <EEPROM.h>
#endif

float DDPVentas1previo = 0;

//Entradas del panel
PanelControl InterruptorVaciadoTiempo(PIN_INTERRUPTOR_VACTIEMPO, INPUT);
PanelControl InterruptorVaciadoPulsacion(PIN_INTERRUPTOR_VACPULSACION, INPUT);
PanelControl InterruptorRecirculacionTiempo(PIN_INTERRUPTOR_RECIRTIEMPO, INPUT);
PanelControl InterruptorRecirculacionPulsacion(PIN_INTERRUPTOR_RECIRPULSACION, INPUT);
PanelControl InterruptorTara(PIN_INTERRUPTOR_TARA, INPUT);
PanelControl InterruptorCalibracion(PIN_INTERRUPTOR_CALIBRACION, INPUT);
PanelControl InterruptorCondIniciales(PIN_INTERRUPTOR_CONDINICIALES, INPUT);
PanelControl InterruptorCierre(PIN_INTERRUPTOR_CIERRE, INPUT);
PanelControl PulsadorBombeo(PIN_PULSADOR_BOMBEO, INPUT);
PanelControl PulsadorStart(PIN_PULSADOR_START, INPUT);
PanelControl PulsadorStop(PIN_PULSADOR_STOP, INPUT);
PanelControl InterruptorManual(PIN_INTERRUPTOR_MANUAL, INPUT);
PanelControl InterruptorEmergencia(PIN_INTERRUPTOR_EMERGENCIA, INPUT);

PanelControl PotenciometroAltura(PIN_POTENCIOMETRO_ALTURA, INPUT);
PanelControl PotenciometroDimensiones(PIN_POTENCIOMETRO_DIMENSIONES, INPUT);


//Salidas del panel
PanelControl LedInicializacion(PIN_LED_INICIALIZACION, OUTPUT);
PanelControl LedFuncionamientoNormal(PIN_LED_FUNCNORMAL, OUTPUT);
PanelControl LedPausa(PIN_LED_PAUSA, OUTPUT);
PanelControl LedEmergencia(PIN_LED_EMERGENCIA, OUTPUT);

PanelControl LedDescargas(PIN_LED_DESCARGAS, OUTPUT);
PanelControl LedAlmacenamiento(PIN_LED_ALMACENAMIENTO, OUTPUT);
PanelControl LedVentas1(PIN_LED_VENTAS1, OUTPUT);
PanelControl LedVentas2(PIN_LED_VENTAS2, OUTPUT);
PanelControl LedFugas(PIN_LED_FUGAS, OUTPUT);




//  Tanques declarados a partir de la clase deposito  // 

/*
 Deposito (int PIN_Rele1_Llenado, int PIN_Rele1_Vaciado, int PIN_IN1, int PIN_IN2, int PIN_ENA, int HX711_dout, int HX711_sck, float valor_calibracion_basculas, int sensor_0, int sensor_1,  int sensor_2, int sensor_3, 
float capacidad_maxima, float vol_max_seguridad, float volumen_descarga_max, float volumen_descarga_min, float t_prox_descarga_max, float t_prox_descarga_min, 
bool UsoDeposito, Deposito *deposito_ant, Deposito *deposito_sig, bool es_fugas, bool es_recarga, float vol_seguridad_anterior, float vol_limite_anterior, float vol_min_comienzo_bomba, Debug *DebugDeposito);
*/

Deposito DepositoRetorno (PIN_RELE_VACIADO_VENTAS1, PIN_RELE_LLENADO_DESCARGAS , NO_EMPLEADO, NO_EMPLEADO, NO_EMPLEADO, NO_EMPLEADO, NO_EMPLEADO, NO_EMPLEADO, NO_EMPLEADO, NO_EMPLEADO, NO_EMPLEADO, NO_EMPLEADO, 
volumen_retorno_limite, volumen_retorno_seguridad, NO_EMPLEADO, NO_EMPLEADO, NO_EMPLEADO, NO_EMPLEADO, DESTINO_DISPENSACION, &DepositoRetorno ,&DepositoRetorno, !FUGAS, !DESCARGAS, NO_EMPLEADO, NO_EMPLEADO, NO_EMPLEADO, NO_EMPLEADO);

Deposito DepositoAlmacenamiento (PIN_RELE_VACIADO_DESCARGAS, PIN_RELE_LLENADO_VENTAS1, NO_EMPLEADO, NO_EMPLEADO, NO_EMPLEADO, dout_almacenamiento, sck_almacenamiento, calibracion_almacenamiento, NO_EMPLEADO, NO_EMPLEADO, NO_EMPLEADO, NO_EMPLEADO,
volumen_almacenamiento_limite, volumen_almacenamiento_seguridad, NO_EMPLEADO, NO_EMPLEADO, NO_EMPLEADO, NO_EMPLEADO, ORIGEN_DISPENSACION, &DepositoAlmacenamiento, &DepositoAlmacenamiento, !FUGAS, !DESCARGAS, NO_EMPLEADO, NO_EMPLEADO, NO_EMPLEADO, NO_EMPLEADO);

Deposito DepositoDescargas (PIN_RELE_LLENADO_DESCARGAS , PIN_RELE_VACIADO_DESCARGAS, NO_EMPLEADO, NO_EMPLEADO, NO_EMPLEADO, NO_EMPLEADO, NO_EMPLEADO, NO_EMPLEADO, PIN_DESCARGAS_SENSOR_NIVEL_0, PIN_DESCARGAS_SENSOR_NIVEL_1, PIN_DESCARGAS_SENSOR_NIVEL_2,
PIN_DESCARGAS_SENSOR_NIVEL_3, volumen_recarga_limite, volumen_recarga_seguridad, volumen_recarga_max, volumen_recarga_min, t_prox_recarga_max, t_prox_recarga_min, ORIGEN_DISPENSACION, &DepositoRetorno, &DepositoAlmacenamiento, !FUGAS, DESCARGAS, NO_EMPLEADO, NO_EMPLEADO, NO_EMPLEADO, NO_EMPLEADO);

Deposito DepositoVentas1 (PIN_RELE_LLENADO_VENTAS1, PIN_RELE_VACIADO_VENTAS1, NO_EMPLEADO, NO_EMPLEADO, NO_EMPLEADO, dout_DepositoVentas1, sck_DepositoVentas1, calibracion_DepositoVentas1, NO_EMPLEADO, NO_EMPLEADO, NO_EMPLEADO, NO_EMPLEADO, volumen_ventas_limite,
volumen_ventas_seguridad, volumen_ventas_max, volumen_ventas_min, t_prox_venta_max, t_prox_venta_min, DESTINO_DISPENSACION, &DepositoAlmacenamiento, &DepositoRetorno, !FUGAS, !DESCARGAS, volumen_almacenamiento_seguridad, volumen_almacenamiento_limite, vol_min_alm_comienzo_bomba, NO_EMPLEADO);

Deposito DepositoVentas2 (PIN_RELE_LLENADO_VENTAS2, PIN_RELE_VACIADO_VENTAS2, NO_EMPLEADO, NO_EMPLEADO, NO_EMPLEADO, dout_DepositoVentas2, sck_DepositoVentas2, calibracion_DepositoVentas2, NO_EMPLEADO, NO_EMPLEADO, NO_EMPLEADO, NO_EMPLEADO, volumen_ventas_limite,
volumen_ventas_seguridad, volumen_ventas_max, volumen_ventas_min, t_prox_venta_max, t_prox_venta_min, DESTINO_DISPENSACION, &DepositoAlmacenamiento, &DepositoRetorno, !FUGAS, !DESCARGAS, volumen_almacenamiento_seguridad, volumen_almacenamiento_limite, vol_min_alm_comienzo_bomba, NO_EMPLEADO);

Deposito DepositoFugas (NO_EMPLEADO, PIN_RELE_VACIADO_FUGAS, PIN_IN1_fuga, PIN_IN2_fuga, PIN_ENA_fuga, dout_fugas, sck_fugas, calibracion_fugas, NO_EMPLEADO, NO_EMPLEADO, NO_EMPLEADO, NO_EMPLEADO, volumen_fugas_limite, volumen_fugas_seguridad,
NO_EMPLEADO, NO_EMPLEADO, t_prox_fuga_max, t_prox_fuga_min, DESTINO_DISPENSACION, &DepositoAlmacenamiento, &DepositoRetorno, FUGAS, !DESCARGAS, NO_EMPLEADO, NO_EMPLEADO, NO_EMPLEADO, NO_EMPLEADO);    //Depósito anterior y siguiente corregido





//Objetos para mensajes de depuración
Debug DebugGeneral(&DepositoDescargas, &DepositoAlmacenamiento, &DepositoVentas1, &DepositoVentas2, &DepositoFugas);  //De momento gestiono todos los mensajes a la vez, pero si me interesase sólo un conjunto de depósitos podría instanciar objetos que 
                                                                                                                      //sólo me den información de ellos (aunque habría poner un NO_EMPLEADO en el lugar de los depósitos que no interesan)



//Para la recepción de emergencia del dashboard
String EntradaSerial = ""; 
bool DatosNuevosSerial = false;




void setup () {
  Serial.begin(9600);
  EntradaSerial.reserve(100); //Se reserva memoria para la entrada serial
  Serial.println("Iniciando...");
  
  //Ahora con todas los depositos declarados, se corrige el puntero a depósito anterior y siguiente
  DepositoRetorno.set_DepositoAnt(&DepositoVentas1);
  DepositoRetorno.set_DepositoSig(&DepositoDescargas);

  DepositoAlmacenamiento.set_DepositoAnt(&DepositoDescargas);
  DepositoAlmacenamiento.set_DepositoSig(&DepositoVentas1);

  DepositoDescargas.set_DebugDeposito(&DebugGeneral);
  DepositoAlmacenamiento.set_DebugDeposito(&DebugGeneral);
  DepositoVentas1.set_DebugDeposito(&DebugGeneral);
  DepositoVentas2.set_DebugDeposito(&DebugGeneral);
  DepositoFugas.set_DebugDeposito(&DebugGeneral);


  //Los relés comienzan apagados (active low)
  digitalWrite (PIN_RELE_LLENADO_DESCARGAS , HIGH);
  digitalWrite (PIN_RELE_VACIADO_DESCARGAS, HIGH);  

  digitalWrite (PIN_RELE_LLENADO_VENTAS1, HIGH); 
  digitalWrite (PIN_RELE_LLENADO_VENTAS2, HIGH);   
 
  digitalWrite (PIN_RELE_VACIADO_VENTAS1, HIGH);
  digitalWrite (PIN_RELE_VACIADO_VENTAS2, HIGH);   
                                                                                                                 
  digitalWrite (PIN_RELE_VACIADO_FUGAS, HIGH);




  randomSeed(analogRead(A4));   //Para los niveles aleatorios de la inicialización y el funcionamiento normal
  DebugGeneral.EnviarMensajeDebug("Saliendo de setup", InstanteActual, EstadoActual);

}






// ------------------------------------------------------------------------------------------------------------------------------------------------------------------------------





void loop () {
  
  InstanteActual = millis();

  DebugGeneral.EnviarMensajeDebug("Inicio de loop", InstanteActual, EstadoActual);


  ActualizarEntradasPanel();
  ActualizarLecturaSensores();


  




                  //  Proceso de Inicialización  //







/********************************************************************************************************************************/
/**************************************************     Pre-Vaciado    **********************************************************/
/********************************************************************************************************************************/
 //A la espera de pulsar Start para empezar
  if (EstadoActual == IDLE_VACIADO){

    DebugGeneral.EnviarMensajeDebug("Estado: Pre-Vaciado", InstanteActual, EstadoActual);

    if (EstadoInterruptorEmergencia == HIGH) {
      ActualizarEstadoGeneral(EMERGENCIA);
    }

    InicializacionVariables();

    //Se invoca actualizar_estado() con un parámetro de entrada ComprobacionInicialControladora a 1 para que todos los depósitos se metan en el estado ComprobacionInicial
    DepositoDescargas.actualizar_estado(InstanteActual, TiempoTotalPausado, EstadoInterruptorEmergencia, LecturaPotenciometroAltura, LecturaPotenciometroDimensiones, EstadoInterruptorCierre, SOLIC_COMPR_INICIAL, EstadoActual);
    DepositoVentas1.actualizar_estado(InstanteActual, TiempoTotalPausado, EstadoInterruptorEmergencia, LecturaPotenciometroAltura, LecturaPotenciometroDimensiones, EstadoInterruptorCierre, SOLIC_COMPR_INICIAL, EstadoActual);
    DepositoVentas2.actualizar_estado(InstanteActual, TiempoTotalPausado, EstadoInterruptorEmergencia, LecturaPotenciometroAltura, LecturaPotenciometroDimensiones, EstadoInterruptorCierre, SOLIC_COMPR_INICIAL, EstadoActual);
    DepositoFugas.actualizar_estado(InstanteActual, TiempoTotalPausado, EstadoInterruptorEmergencia, LecturaPotenciometroAltura, LecturaPotenciometroDimensiones, EstadoInterruptorCierre, SOLIC_COMPR_INICIAL, EstadoActual); 
    


    DebugGeneral.EnviarMensajeDebug("Listo para comenzar Proceso de Inicialización", InstanteActual, EstadoActual);

    if ((EstadoInterruptorManual == DIAL_AUTOMATICO) || ((EstadoInterruptorManual == DIAL_MANUAL) && (FlancoPulsadorStart == 1))){
      ActualizarEstadoGeneral(VACIADO);
    }

    
  
  }



/********************************************************************************************************************************/
/****************************************************     Vaciado    ************************************************************/
/********************************************************************************************************************************/
 //Al entrar en esta etapa, no sabemos a qué nivel está cada tanque

  if (EstadoActual == VACIADO){



    if (EstadoInterruptorEmergencia == HIGH) {
      ActualizarEstadoGeneral(EMERGENCIA);
    }

    DebugGeneral.EnviarMensajeDebug("Estado: VACIADO", InstanteActual, EstadoActual);

    if (EstadoInterruptorVaciadoTiempo == HIGH) {
      DepositosVaciados = VaciarDepositosTiempo();   //la función hace el vaciado y devuelve un 1 cuando acaba

      if (DepositosVaciados){

        ActualizarEstadoGeneral(RECIRCULACION); 
      }


    } else if (EstadoInterruptorVaciadoPulsacion == HIGH) {
      VaciarDepositosPulsacion();

      if (FlancoPulsadorStop == 1){
        Selector = 0;
        ActualizarEstadoGeneral(RECIRCULACION); 
      }
      

    } else {                                      //BotoneraVaciadoPulsacion == LOW   &&   BotoneraVaciadoTiempo == LOW
      ActualizarEstadoGeneral(RECIRCULACION); 
    }

    //Poner pulsador a 0 para pasar a recirculacion
    if (FlancoPulsadorStop == 1){
    FlancoPulsadorStop = 0;
    }


  }

  



/********************************************************************************************************************************/
/************************************************     Recirculacion    **********************************************************/
/********************************************************************************************************************************/
//Al entrar en esta etapa, se supone que que todos los tanques están a un nivel muy bajo, e incluso completamente vacíos

  if (EstadoActual == RECIRCULACION) {



    if (EstadoInterruptorEmergencia == HIGH) {
      ActualizarEstadoGeneral(EMERGENCIA);
    }

    DebugGeneral.EnviarMensajeDebug("Estado: RECIRCULACION", InstanteActual, EstadoActual);

    if (EstadoInterruptorRecirculacionTiempo == HIGH) {

		  DepositosRecirculados = RecircularDepositosTiempo(); 

      if (DepositosRecirculados){
        ActualizarEstadoGeneral(TARA);
      }

	  } else if (EstadoInterruptorRecirculacionPulsacion == HIGH) {

      RecircularDepositosPulsacion();

		  if (FlancoPulsadorStop == 1){
        Selector = 0;
        ActualizarEstadoGeneral(TARA);
		  }
		
    } else {
      ActualizarEstadoGeneral(TARA);
    }


  }






/********************************************************************************************************************************/
/*****************************************************     Tarar    *************************************************************/
/********************************************************************************************************************************/
//Al entrar en esta etapa, se supone que todos los depósitos tienen únicamente el fondillo

  if (EstadoActual == TARA) {    

    if (EstadoInterruptorEmergencia == HIGH) {
      ActualizarEstadoGeneral(EMERGENCIA);
    }
    
    DebugGeneral.EnviarMensajeDebug("Estado: TARA", InstanteActual, EstadoActual);
	
    if (EstadoInterruptorTara == HIGH) {
      bool TaraAlmacenamiento = DepositoAlmacenamiento.realizar_tara();
      bool TaraVentas1 = DepositoVentas1.realizar_tara();
      bool TaraVentas2 = DepositoVentas2.realizar_tara();
      bool TaraFugas = DepositoFugas.realizar_tara(); 
 
      if (TaraVentas1 && TaraVentas2 && TaraAlmacenamiento && TaraFugas) {
        ActualizarEstadoGeneral(CALIBRACION);
        DebugGeneral.EnviarMensajeDebug("Tara 1 realizada", InstanteActual, EstadoActual);
        DebugGeneral.EnviarMensajeDebug("Pasando a Calibración", InstanteActual, EstadoActual);
      }
 
      

    } else {
      DepositoAlmacenamiento.realizar_tara(false); 
      DepositoVentas1.realizar_tara(false);
      DepositoVentas2.realizar_tara(false);
      DepositoFugas.realizar_tara(false);
      ActualizarEstadoGeneral(CALIBRACION);   
    }
      
  }







/********************************************************************************************************************************/
/*****************************************************     Calibrar    **********************************************************/
/********************************************************************************************************************************/
//Al entrar en esta etapa, como en la anterior no hubo cambios, se supone que todos los tanque tienen únicamente el fondillo


  if (EstadoActual == CALIBRACION) {   

    if (EstadoInterruptorEmergencia == HIGH) {
      ActualizarEstadoGeneral(EMERGENCIA);
    }

    DebugGeneral.EnviarMensajeDebug("Estado: CALIBRACION", InstanteActual, EstadoActual);

    if (EstadoInterruptorCalibracion == HIGH) {
      DepositosCalibrados = CalibrarDepositos();
      
      if (DepositosCalibrados){

        ActualizarEstadoGeneral(COND_INICIALES);
      }

    } else {
      ActualizarEstadoGeneral(COND_INICIALES);
    }

  }





/********************************************************************************************************************************/
/*************************************************     Cond. Iniciales    *******************************************************/
/********************************************************************************************************************************/
//Al entrar en esta etapa, todos los tanques tienen únicamente el fondillo, a excepción del depósito principal, que además tiene un volumen de descarga de nivel 2

  if (EstadoActual == COND_INICIALES) {

    
    if (EstadoInterruptorEmergencia == HIGH) {
      ActualizarEstadoGeneral(EMERGENCIA);
    }

    DebugGeneral.EnviarMensajeDebug("Estado: COND_INICIALES", InstanteActual, EstadoActual);

    if (EstadoInterruptorCondIniciales == HIGH) {

      CondInicEstablecidas = EstablecerCondInic();
      
      if (CondInicEstablecidas){
        ActualizarEstadoGeneral(IDLE_FUNC_NORMAL);
      }

    } else {
      ActualizarEstadoGeneral(IDLE_FUNC_NORMAL);
    }

  }




/********************************************************************************************************************************/
/*********************************************     Pre-Funcionamiento Normal    *************************************************/
/********************************************************************************************************************************/

  if (EstadoActual == IDLE_FUNC_NORMAL){

    
    if (EstadoInterruptorEmergencia == HIGH) {
      ActualizarEstadoGeneral(EMERGENCIA);
    }

    DebugGeneral.EnviarMensajeDebug("Listo para comenzar Funcionamiento Normal", InstanteActual, EstadoActual);

    if ((EstadoInterruptorManual == DIAL_AUTOMATICO) || ((EstadoInterruptorManual == DIAL_MANUAL) && (FlancoPulsadorStart == 1))){
      ActualizarEstadoGeneral(FUNC_NORMAL);
    }
  }











//**************************************  FUNCIONAMIENTO NORMAL  *****************************************************************************************
  if (EstadoActual == FUNC_NORMAL) {


    
    if ((EstadoInterruptorEmergencia == LOW) && (FlancoPulsadorStop == HIGH)) {            
      
      if (InstanteComienzoPausa == 0){    //Si InstanteComienzoPausa es 0, quiere decir que o bien aún no ha sucedido una Pausa, o bien ya hemos sumado el tiempo de pausa anterior a TiempoTotalPausado
        InstanteComienzoPausa = InstanteActual;
      }
      ActualizarEstadoGeneral(PAUSA);
    }
      
    emergencia_recarga = DepositoDescargas.actualizar_estado(InstanteActual, TiempoTotalPausado, EstadoInterruptorEmergencia,  LecturaPotenciometroAltura, LecturaPotenciometroDimensiones, EstadoInterruptorCierre, !SOLIC_COMPR_INICIAL, EstadoActual);  
    emergencia_disp_1 = DepositoVentas1.actualizar_estado(InstanteActual, TiempoTotalPausado, EstadoInterruptorEmergencia,  LecturaPotenciometroAltura, LecturaPotenciometroDimensiones, EstadoInterruptorCierre, !SOLIC_COMPR_INICIAL, EstadoActual);
    emergencia_disp_2 = DepositoVentas2.actualizar_estado(InstanteActual, TiempoTotalPausado, EstadoInterruptorEmergencia,  LecturaPotenciometroAltura, LecturaPotenciometroDimensiones, EstadoInterruptorCierre, !SOLIC_COMPR_INICIAL, EstadoActual);
    emergencia_fugas = DepositoFugas.actualizar_estado(InstanteActual, TiempoTotalPausado, EstadoInterruptorEmergencia,  LecturaPotenciometroAltura, LecturaPotenciometroDimensiones, EstadoInterruptorCierre, !SOLIC_COMPR_INICIAL, EstadoActual);
    
    if ((emergencia_recarga == true) || (emergencia_disp_1 == true) || (emergencia_disp_2 == true) || (emergencia_fugas == true) || (EstadoInterruptorEmergencia == HIGH)) {
      ActualizarEstadoGeneral(EMERGENCIA);
    }


    if(DepositoDescargas.get_PausaSumada() && DepositoVentas1.get_PausaSumada() && DepositoVentas2.get_PausaSumada()){
      TiempoTotalPausado = 0;
    }



    if (((EstadoPulsadorStop == LOW) && (EstadoInterruptorEmergencia == LOW) && (EstadoInterruptorCierre == HIGH)) || InstanteActual >= TiempoSimMax ) {
      ActualizarEstadoGeneral(FIN_EXPERIMENTO);
                                 
    }
    


  }


//*******************************************  PAUSA  *****************************************************************************************
  if (EstadoActual == PAUSA) {

    if (EstadoInterruptorEmergencia == HIGH) {
      ActualizarEstadoGeneral(EMERGENCIA);
    }

    if (InstanteComienzoPausa == 0){                //Si acabamos de entrar en Pausa desde funcionamiento normal, se registra el instante de comienzo de la pausa.
      InstanteComienzoPausa = InstanteActual;
    }
      
    
    DepositoDescargas.cerrar_valvula_llenado();
    DepositoDescargas.cerrar_valvula_vaciado();
    DepositoVentas1.cerrar_valvula_llenado();
    DepositoVentas1.cerrar_valvula_vaciado();     
    DepositoVentas2.cerrar_valvula_llenado();
    DepositoVentas2.cerrar_valvula_vaciado(); 

    if ((EstadoPulsadorStop == LOW) && (EstadoInterruptorEmergencia == LOW) && (FlancoPulsadorStart == HIGH)) {    
      
      TiempoTotalPausado += InstanteActual - InstanteComienzoPausa;  // Se calcula el tiempo en PAUSA
      InstanteComienzoPausa = 0;                                     // Se resetea el InstanteComienzoPausa para que se pueda asignar al instante correspondiente de sucesivas pausas

      DepositoDescargas.set_PausaSumada(false); 
      DepositoVentas1.set_PausaSumada(false); 
      DepositoVentas2.set_PausaSumada(false); 
      DepositoFugas.set_PausaSumada(false); 

      
      ActualizarEstadoGeneral(FUNC_NORMAL); 
                                      
    }

    if ((EstadoPulsadorStart == LOW) && (EstadoInterruptorEmergencia == LOW) && (EstadoInterruptorCierre == HIGH)) {
      ActualizarEstadoGeneral(FIN_EXPERIMENTO);
                                 
    }


  }
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

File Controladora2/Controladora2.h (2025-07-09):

//  DECLARACION DE VARIABLES  //

//Las variables no inicializadas a un valor, se inicializan automáticamente a 0

#ifndef Controladora2_h
#define Controladora2_h



#include "Arduino.h"


const int NO_EMPLEADO = 0;
const int DESTINO_DISPENSACION = 0;
const int ORIGEN_DISPENSACION = 1;
const bool DESCARGAS = 1;
const bool FUGAS = 1;

const bool SOLIC_COMPR_INICIAL = 1;



//  Tiempos utilizados  //

unsigned long InstanteActual;
unsigned long TiempoTotalPausado = 0;
const unsigned long TiempoSimMax = 3600000;     //1 hora en ms



unsigned long InstanteDatalogger = 0;                               //  Instante en el que se realizó el Datalogging
#define T_INTERVALO_DATALOGGER 20000                         






//  Sensores 

#define PIN_DESCARGAS_SENSOR_NIVEL_0 8                                    
#define PIN_DESCARGAS_SENSOR_NIVEL_1 9                                       
#define PIN_DESCARGAS_SENSOR_NIVEL_2 10                                 
#define PIN_DESCARGAS_SENSOR_NIVEL_3 11                                 

#define dout_almacenamiento 27                               
#define sck_almacenamiento 26                                    
float calibracion_almacenamiento = 13000;                    

#define dout_DepositoVentas1 35                               
#define sck_DepositoVentas1 34
float calibracion_DepositoVentas1 = 268000;                  

#define dout_DepositoVentas2 36                                 
#define sck_DepositoVentas2 37
float calibracion_DepositoVentas2 = 264000;                     

#define dout_fugas 38                                         
#define sck_fugas 39
float calibracion_fugas = 310000;                               



//  Actuadores

const int PIN_RELE_VACIADO_DESCARGAS = 52;        // RELÉ 9
const int PIN_RELE_LLENADO_VENTAS1 = 51;          // RELÉ 10
const int PIN_RELE_LLENADO_VENTAS2 = 50;          // RELÉ 11
const int PIN_RELE_VACIADO_FUGAS = 47;            // RELÉ 14
const int PIN_RELE_VACIADO_VENTAS1 = 49;          // RELÉ 12
const int PIN_RELE_VACIADO_VENTAS2 = 48;          // RELÉ 13
const int PIN_RELE_LLENADO_DESCARGAS = 28;        // RELÉ 8

#define PIN_ENA_fuga 46                                        
#define PIN_IN1_fuga 45                                                                
#define PIN_IN2_fuga 53    

#define PWM_MAX 255



//  Volúmenes

float volumen_recarga_limite = 33;                         
float volumen_recarga_seguridad = 30;                      

float volumen_almacenamiento_seguridad = 100;               
float volumen_almacenamiento_limite = 125;                   
float vol_min_alm_comienzo_bomba = 2;                   

float volumen_ventas_limite = 2.2;                            
float volumen_ventas_seguridad = 2;                        

float volumen_fugas_limite = 2.2;                            
float volumen_fugas_seguridad = 2;                         

float volumen_retorno_limite = 150;
float volumen_retorno_seguridad = 125;



//  Distribuciones aleatorias de dispensaciones

#define volumen_recarga_min 5                              
#define volumen_recarga_max 25 
#define volumen_ventas_min 0.5                               
#define volumen_ventas_max 1.6                             
#define t_prox_recarga_min 20000   // ANTES 30000                          
#define t_prox_recarga_max 40000        // ANTES 50000                      
#define t_prox_venta_min 15000           // ANTES 10000                   
#define t_prox_venta_max 25000// ANTES 20000
#define t_prox_fuga_min 60000
#define t_prox_fuga_max 120000



//  Variables de simulación //
bool emergencia_recarga; 
bool emergencia_disp_1;
bool emergencia_disp_2;
bool emergencia_fugas;

bool ConjuntoListoParaReiniciar;




//  PANEL DE CONTROL  //

//Pines de entradas del panel
const int PIN_INTERRUPTOR_VACTIEMPO = 16;
const int PIN_INTERRUPTOR_VACPULSACION = 17;
const int PIN_INTERRUPTOR_RECIRTIEMPO = 18;
const int PIN_INTERRUPTOR_RECIRPULSACION = 19;
const int PIN_INTERRUPTOR_TARA = 20;
const int PIN_INTERRUPTOR_CALIBRACION = 21;
const int PIN_INTERRUPTOR_CONDINICIALES = 22;
const int PIN_INTERRUPTOR_CIERRE = 32;
const int PIN_PULSADOR_BOMBEO = 25;
const int PIN_PULSADOR_START = 31;
const int PIN_PULSADOR_STOP = 33;
const int PIN_INTERRUPTOR_MANUAL = 24;
const int PIN_INTERRUPTOR_EMERGENCIA = 23;
const int PIN_POTENCIOMETRO_ALTURA = A3;
const int PIN_POTENCIOMETRO_DIMENSIONES = A1;

//Pines de salidas del panel
const int PIN_LED_INICIALIZACION = 14;
const int PIN_LED_FUNCNORMAL = 15;
const int PIN_LED_PAUSA = 41;
const int PIN_LED_EMERGENCIA = 42;
const int PIN_LED_DESCARGAS = 6;
const int PIN_LED_ALMACENAMIENTO = 5;
const int PIN_LED_VENTAS1 = 4;
const int PIN_LED_VENTAS2 = 3;
const int PIN_LED_FUGAS = 2;


//Señales correspondientes a las entradas del panel
int EstadoInterruptorVaciadoTiempo;
int FlancoInterruptorVaciadoTiempo;
int EstadoInterruptorVaciadoPulsacion;
int FlancoInterruptorVaciadoPulsacion;
int EstadoInterruptorRecirculacionTiempo;
int FlancoInterruptorRecirculacionTiempo;
int EstadoInterruptorRecirculacionPulsacion;
int FlancoInterruptorRecirculacionPulsacion;
int EstadoInterruptorTara;
int FlancoInterruptorTara;
int EstadoInterruptorCalibracion;
int FlancoInterruptorCalibracion;
int EstadoInterruptorCondIniciales;
int FlancoInterruptorCondIniciales;
int EstadoInterruptorCierre;
int FlancoInterruptorCierre;
int EstadoPulsadorBombeo;
int FlancoPulsadorBombeo;
int EstadoPulsadorStart;
int FlancoPulsadorStart;
int EstadoPulsadorStop;
int FlancoPulsadorStop;
int EstadoInterruptorManual;
int FlancoInterruptorManual;
int EstadoInterruptorEmergencia;
int FlancoInterruptorEmergencia;
int LecturaPotenciometroAltura;
int LecturaPotenciometroDimensiones;

const int DIAL_AUTOMATICO = 0;
const int DIAL_MANUAL = 1;

const int PARPADEO_LENTO = 0;
const int PARPADEO_RAPIDO = 1;
const int PARPADEO_ERROR = 2;



// INICIALIZACIÓN y FUNCIONAMIENTO NORMAL //


//  ActualizarLecturaSensores()  //
bool DescargasSensorNivel0;
bool DescargasSensorNivel1;
bool DescargasSensorNivel2;
bool DescargasSensorNivel3;




//Variables de estado
const int IDLE_VACIADO = 0;
const int VACIADO = 1;
const int RECIRCULACION = 2;
const int TARA = 3;
const int CALIBRACION = 4;
const int COND_INICIALES = 5;
const int IDLE_FUNC_NORMAL = 6;
const int FUNC_NORMAL = 7;
const int EMERGENCIA = 29;
const int PAUSA = 30;
const int FIN_EXPERIMENTO = 31;      //o CIERRE

int EstadoActual;


//Vaciado
bool DepositosVaciados;
int Selector;

//Recirculacion
bool DepositosRecirculados;

//Calibrar
bool DepositosCalibrados;

//Cond Iniciales
bool CondInicEstablecidas;






//  VaciarDepositosTiempo()  //
const int VACIADO_ABRIENDO_INFERIORES = 8;
const int VACIADO_ABRIENDO_SUPERIORES = 9;
const int VACIANDO_TODOS = 10;

int EstadoVaciadoT = VACIADO_ABRIENDO_INFERIORES;
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

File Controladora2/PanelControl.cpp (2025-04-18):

//PanelControl.cpp

#include "Arduino.h"
#include "PanelControl.h"


//Constantes empleadas
const int ERROR_ENTRADA_PANEL = 2;

const int TIEMPO_REBOTE_PRED = 50;

const int PARPADEO_LENTO = 0;
const int PARPADEO_RAPIDO = 1;
const int PARPADEO_ERROR = 2;

const unsigned long TIEMPO_PARPADEO_RAPIDO = 250;
const unsigned long TIEMPO_ON_PARPADEO_LENTO  = 500;
const unsigned long TIEMPO_OFF_PARPADEO_LENTO  = 1000;
const unsigned long TIEMPO_PARPADEO_ERROR  = 1500;

const float LED_UMBRAL_INF_INTERVALO1 = 0.10;
const float LED_UMBRAL_INF_INTERVALO2 = 0.30;
const float LED_UMBRAL_INF_INTERVALO3 = 0.60;
const float LED_UMBRAL_INF_INTERVALO4 = 0.75;
const float LED_UMBRAL_INF_INTERVALO5 = 0.90;

const int MAX_PWM = 255;
const float UMBRAL_25 = 0.25;
const float UMBRAL_50 = 0.50;
const float UMBRAL_75 = 0.75;





PanelControl::PanelControl(int Pin, int Tipo) {  
	_Pin = Pin;
	_Tipo = Tipo;     //INPUT o OUTPUT
	_EstadoAnterior = LOW;
	_InstanteAnteriorRebote = 0;
	_TiempoRebote = TIEMPO_REBOTE_PRED;
  
	pinMode(_Pin, _Tipo);
}


int PanelControl::ComprobarEstado() {
	if (_Tipo == INPUT){
		_EstadoActual = digitalRead(_Pin);
		return _EstadoActual;  
	} else {
		return ERROR_ENTRADA_PANEL;   //Devuelvo un 2 (en forma de const global) para que no se confunda con una entrada de verdad
	}

}


int PanelControl::ComprobarFlanco(unsigned long InstanteActual) {
	//No hay "if (_Tipo == INPUT)" porque lo primero que hago aquí es invocar ComprobarEstado(), que ya tiene ese if
	
  _InstanteActual = InstanteActual;
	_EstadoActual = ComprobarEstado();

	if(_EstadoActual == _EstadoAnterior) {
    return 0;
  }

	if((_InstanteActual - _InstanteAnteriorRebote) < _TiempoRebote) {  
    return 0;                                                        
	}

	if(_EstadoActual > _EstadoAnterior) {
    _Flanco = 1;
  } else {
    _Flanco = -1;
  }

  _EstadoAnterior = _EstadoActual;
  _InstanteAnteriorRebote = _InstanteActual;

  return _Flanco;

}



int PanelControl::LeerValor() {                 //Para entradas analógicas
	if (_Tipo == INPUT){
		_LecturaActual= analogRead(_Pin);
		return _LecturaActual;  
	} else {
		return ERROR_ENTRADA_PANEL;  
	}

}




void PanelControl::Encender() {
	if (_Tipo == OUTPUT){
    //Serial.println("Se mete en el condicional de _Tipo");
		digitalWrite(_Pin, HIGH);
	} else {
    return ERROR_ENTRADA_PANEL;
	}

}



void PanelControl::Apagar() {
	if (_Tipo == OUTPUT){
		digitalWrite(_Pin, LOW);
	} else {
    return ERROR_ENTRADA_PANEL;
	}

}





void PanelControl::Parpadear(int TipoParpadeo, unsigned long InstanteActual) {  // El led parpadeará a distintas frecuencias en función del parámetro de entrada PARPADEO_RAPIDO, PARPADEO_LENTO o PARPADEO_ERROR.
                                    // Los tiempos son: TIEMPO_PARPADEO_RAPIDO = 250, TIEMPO_ON_PARPADEO_LENTO = 500, TIEMPO_OFF_PARPADEO_LENTO = 1000, TIEMPO_PARPADEO_ERROR = 1500
  
  _TipoParpadeo = TipoParpadeo;
  _InstanteActual = InstanteActual;

  if(_TipoParpadeo == PARPADEO_RAPIDO) {

    // Comprobar si ha pasado el tiempo suficiente para cambiar el estado del parpadeo, ya sea estando encendido o apagado
    if ((_InstanteActual - _InstanteUltimoCambioParpadeo) >= TIEMPO_PARPADEO_RAPIDO) {
      
      _ParpadeoEncendido = !_ParpadeoEncendido;  // Cambiar el estado del parpadeo
      _InstanteUltimoCambioParpadeo = _InstanteActual;  // Actualizar el tiempo del último cambio de estado

      if (_ParpadeoEncendido) {
        Encender(); 
        
      } else {
        Apagar();  
      }
    }
  

  } else if (_TipoParpadeo == PARPADEO_LENTO) {
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

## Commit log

2025-04-18 Se agrega el codigo
2025-06-14 Archivos 3D para carril DIN
    [Montura Arduino Mega DIN.stl, Montura Peristaltica.3mf, Montura Relés.3mf]
2025-06-18 Actualización de código
2025-07-09 Modelo 3d de la planta final
